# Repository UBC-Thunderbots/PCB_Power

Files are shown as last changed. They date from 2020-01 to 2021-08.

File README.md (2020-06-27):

# PCB_Power README

## Description

This repository contains Altium PCB files for UBC Thunderbots' power pcb. Anyone who wishes to push changes to this project must get permission from the current Electrical Team Lead.

## Getting Started

### Required software

1. git
2. Altium Designer

### Instructions

1. Either create a new working branch or select an existing branch other than `master`.
2. **Recursively clone** (`git clone --recurse-submodules`) your working branch of the repository to your PC (i.e. `C:/Documents/thunderbots/PCB_Power`).
3. In Altium Designer, navigate to *Preferences -> Data Management -> Version Control* and ensure **SVN - Subversion** is enabled and **Version 1.9** is selected.
4. In Altium Designer, navigate to *Preferences -> Data Management -> Design Repositories*.
5. Within *Design Repositories* click on on *Connect To* -> **SVN**.
6. In the dialogue box that comes up, fill in the following information:

Field|Selection/Input
---|---
Name|PCB_Power
Default Checkout Path|location of local repository (i.e. `C:/Documents/thunderbots/PCB_Power`)
Method|https
Server|github.com
Server Port|Default
Repository Subfolder|/UBC-Thunderbots/PCB_Power
User Name|*your github login username*
Password|*your github login password*

7. Click **Test**.

After your repository is connected, you can add or remove files like a regular Altium Project folder and then commit and push your changes to the remote repository.

[Reference](https://forum.live.altium.com/#posts/235981/718003)

### Altium_Libraries Submodule Integration

To enforce component and board compatibility, the Altium_Libraries repository is integrated as a submodule. Before making changes to a project, **ensure that your local `Altium_Libraries/` submodule is current**. This can be done using `git submodule update` in git bash.

## Repository Structure

At the highest level, there should be the most up to date board revisions, (e.g.
`power-v1.0/`), `archive/`, and `Altium_Libraries/`. Any previous versions should be placed in `archive/`. Every board revision directory should abide by the following structure:

```
<name-v#>/
├── doc/
│   ├── <name>.pdf
│   └── <name>.xslx or <name>.csv
├── pcb/
│   ├── guidelines/
│   ├── <name>.PrjPCB
│   ├── <name>.SchDoc
│   └── <name>.PcbDoc
└── sim/
```

### doc/

For documentation and relevant non-simulation and layout files. This includes PDFs of the design and bills of materials (`*.xlsx` or `.csv` format).

### pcb/

For any PCB design software files related to the schematic capture and PCB layout of board. This includes schematic and PCB layout guidelines (`guidelines/`).

### sim/

For any simulation files related to the PCB design here.

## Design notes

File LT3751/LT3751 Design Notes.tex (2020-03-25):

\documentclass{article}
\usepackage{amsmath}
\usepackage{fullpage}
\usepackage{graphicx}

\title{LT3751 Design Notes}
\author{Graham Whyte}

\begin{document}
	\maketitle
	\noindent This document will contain the design process for the LT3751 flyback converter. It is to be used alongside (not in place of) the LT3751 data sheet. Thunderbots uses this converter as a 24V - 240V capacitor charger. \\
	
	\begin{figure}[h!]
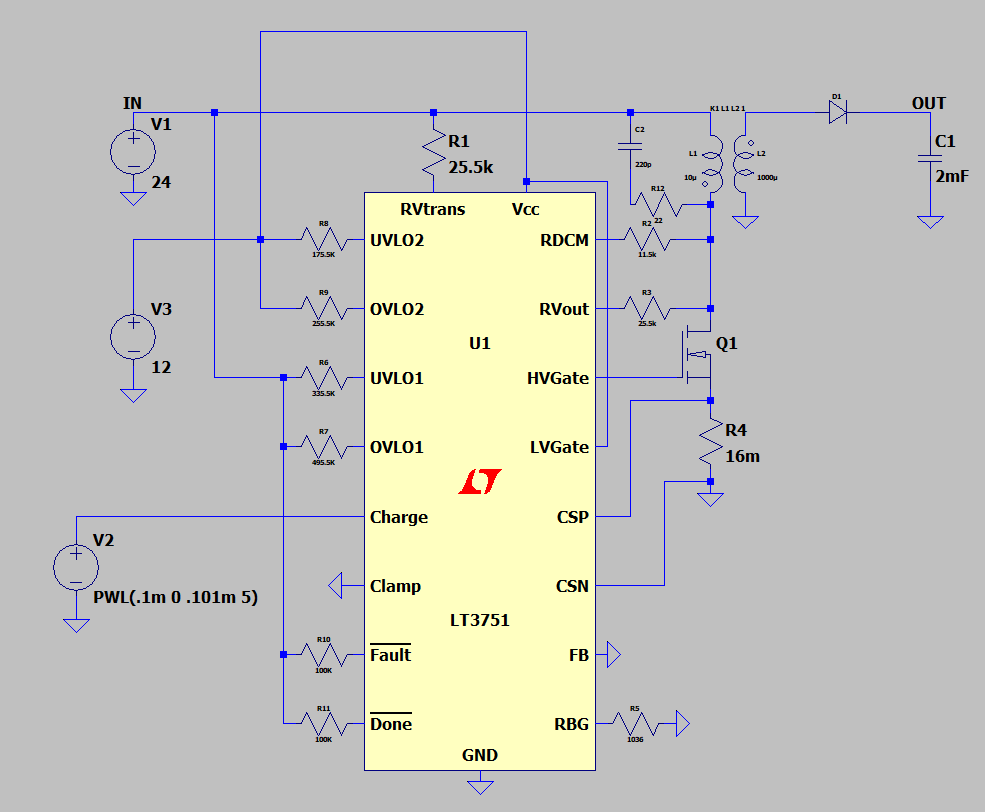
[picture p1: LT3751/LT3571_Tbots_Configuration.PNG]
		
	\end{figure}
	
	\noindent The following variables were selected as design parameters:
	
	\begin{table}[h]
		\centering
		\begin{tabular}{lll}
			\textbf{Parameter}   & \textbf{Description}                      & \textbf{Value} \\
			\hline
			$V_{trans}$ & Transformer supply voltage       & 24V   \\
			$V_{out}$   & Output voltage                   & 240V  \\
			$C_{out}$   & Output capacitance               & 2mF   \\
			$I_{pk}$    & Peak transformer primary current & 10A  \\
			$VCC$		& Supply Voltage				   & 12V
		\end{tabular}
		\centering
	\end{table}
	
	\section{Pins}
	This section will briefly describe each pin and the calculations of any necessary components.\\
	
	\noindent \textbf{Note: Resistor values are calculated values and need to be updated with standard resistor values}
	
	\subsection{RVtrans}
	RVtrans is used as the transformer supply sense pin. The resistor $R_{trans}$ is placed between $V_{trans}$ and the pin. See Section 2 for instructions on setting $RV_{trans}$.
	
	\subsection{UVLO1, OVLO1, UVLO2, OVLO2}
	These four pins serve similar purposes, so they will be covered in the same section. UVLO1 and OVLO1 are the $V_{trans}$ undervoltage/overvoltage detection pins and will raise a fault signal when $V_{trans}$ drops below 18V or goes above 26V. They are connected to $V_{trans}$ via $R_{UVLO1}$ and $R_{OVLO1}$, which are calculated as per page 7 of the data sheet:
	\[R_{UVLO1} = \dfrac{V_{UVLO1} - 1.225V}{50\mu A} = \dfrac{18V - 1.225V}{50\mu A} = 335.5k\Omega\]
	\[R_{OVLO1} = \dfrac{V_{OVLO1} - 1.225V}{50\mu A} = \dfrac{26V - 1.225V}{50\mu A} = 495.5k\Omega\]
	UVLO2 and OVLO2 are the VCC undervoltage/overvoltage detection pins and will raise a fault signal when $VCC$ drops below 10V or goes above 14V. They are connected to $VCC$ via $R_{UVLO2}$ and $R_{OVLO2}$ which are calculated as follows:
	\[R_{UVLO2} = \dfrac{V_{UVLO2} - 1.225V}{50\mu A} = \dfrac{10V - 1.225V}{50\mu A} = 175.5k\Omega\]
	\[R_{OVLO2} = \dfrac{V_{OVLO2} - 1.225V}{50\mu A} = \dfrac{14V - 1.225V}{50\mu A} = 255.5k\Omega\]
	
	\subsection{Fault}
	This (active low) pin goes low when an undervoltage or overvoltage condition occurs and all switching will be disabled. The charge pin must be toggled to reset this signal. This pin must be pulled up to $V_{trans}$ or $VCC$ via a 100k$\Omega$ resistor.
	
	\subsection{Done}
	This (active low) pin goes low when the target output voltage is reached or the fault pin goes low. The charge pin must be toggled to reset this signal. This pin must be pulled up to $V_{trans}$ or $VCC$ via a 100k$\Omega$ resistor.
	
	\subsection{Charge}
	Drive pin higher than 1.5V to start charging. Bring to below 0.3V to stop charging. This pin is directly controlled by the microcontroller.
	
	\subsection{Clamp}
	Clamps the gate driver pin voltage. Clamp is set to 5.6V if this pin is connected to $VCC$ and 10.5V if connected to ground. In our implementation, $V_{GS}$ of our NMOS transistor is 10V so Clamp is connected to GND.
	
	\subsection{FB}
	Feedback regulation pin. The voltage of this pin determines whether the LT3571 is used as a no-load voltage regulator, heavy load voltage regulator, or capacitor charger. We connect this pin to ground for capacitor charger mode.
	
	\subsection{CSN and CSP}
	Negative and positive NMOS source current sense pins. Connect CSP to the source of the external transistor and CSN to ground, then connect a source resistor between CSP and CSN to complete the circuit. The value of this sense resistor is important as it sets the maximum value of the source current through the transistor, which by extension is the current through the transformer primary ($I_{pk}$). This resistor is calculated as follows:
	\[R_{CS} = \dfrac{106mV}{I_{pk}} = \dfrac{106mV}{10A} = 16m\Omega\]
	
	\subsection{VCC}
	12V input from the voltage regulator. Bypass with a XR5 ceramic cap because the data sheet says so.
	
	\subsection{LVGate}
	Low voltage gate pin. If $VCC$ is less than 8V, connect to external transistor gate. Otherwise connect to $VCC$. Our $VCC$ is 12V so this pin is connected to $VCC$. 
	
	\subsection{HVGate}
	High voltage gate pin. Connect to external transistor gate. Will drive gate voltage to within $VCC$-2V. Gets clamped based on the state of the Clamp pin.
	
	\subsection{RBG}
	This pin is really important because it sets the output voltage! Connect to ground via the $R_{BG}$ resistor. See section 2 for instructions on setting this resistor value.
	
	\subsection{RVout}
	Output voltage sense pin. Pretty self-explanatory. Connect to the external NMOS drain via the $R_{out}$ resistor. See section 2 for instructions on setting this resistor value.
	
	\subsection{RDCM}
	Discontinuous mode sense pin. Determines when to initiate the next switch cycle. Connect to the external NMOS drain via the $R_{DCM}$ resistor. See section 2 for instructions on setting this resistor value.
	
	\subsection{GND}
	Don't worry about it.
	
	\section{External Resistors}
	\subsection{RTrans, Rout, and RDCM}
	The values of $R_{trans}, R_{out}, \text{and } R_{DCM}$ are set based on $V_{trans}$ and $\Delta V_{Drain}$, where $\Delta V_{Drain}$ is the difference between $V_{Drain}$ (the drain of the external NMOS) and $V_{trans}$. $V_{Drain}$ is just $V_{out}$ + $V_{out}$ reflected back over the primary. 
	\[V_{Drain} = V_{trans} + \dfrac{V_{out}}{n} = 24V + \dfrac{240V}{10} = 48V\]
	We use this value for $\Delta V_{Drain}$:
	\[\Delta V_{Drain} = V_{Drain} - V_{trans} = 48V - 24V = 24V\]
	and compare it to Table 2 in the data sheet (pg 17):
	
	\begin{figure}[h!]
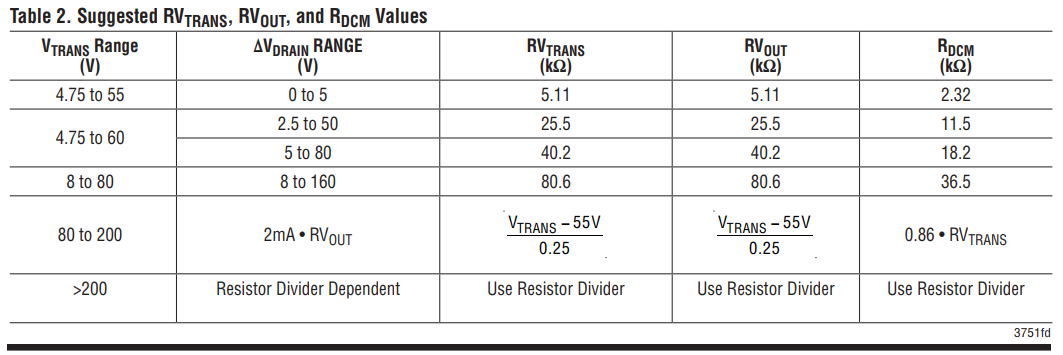
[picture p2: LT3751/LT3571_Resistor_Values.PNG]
		
	\end{figure}

	\noindent Based on the table, $R_{trans} = 25.5k\Omega, R_{out} = 25.5k\Omega, \text{and } R_{DCM} = 11.5k\Omega$. These are also the values RoboJackets use so that's probably a good sign.

	\subsection{RBG}
	With the other resistors selected, $R_{BG}$ is calculated as follows (as per pg 45 of the data sheet):
	\[R_{BG} = 0.98N\dfrac{RV_{out}}{V_{out} + V_{diode}} = 0.98(10)\dfrac{25.5k\Omega}{240V + 1.7V} = 1033.9\Omega\]
	Where N is based on the flyback transformer (section 3.1) and $V_{diode}$ is the forward voltage of the output diode (section 3.2).
	
	\section{External Components}
	\subsection{Flyback Transformer}
	$I_{pk}$ is the main criteria for selecting the transformer. The CoilCraft DA-2034-AL is one of the transformers recommended by the LT3751 manufacturers (table 1 of the data sheet). It is the current frontrunner because of its ability to handle up to 10A on the primary, 1:10 ratio, and relatively small size. \textbf{Not available on digikey though (is available on Mouser).} This transformer is currently used by RoboJackets, while the similar CoilCraft DA-2032-AL is used by Mannheim ($I_{pk} = 5A$ for this transformer).
	\subsection{Output Diode}
	The output diode is selected based on the maximum repetitive reverse voltage ($V_{RRM}$) and the average forward current $I_{Av}$. The diode must meet the following requirements:
	\[V_{RRM} > V_{out} + N*V_{trans} = 240V + 10(24V)  = 480V\]
	\[I_{Av} > \dfrac{I_pk}{2N} = \dfrac{10A}{2*20} = 0.5A\]  
	The Fairchild ES3J is one of the diodes recommended by the LT3751 manufacturers (table 4 in the data sheet). It meets our requirements and has a low $t_{rr}$.
	\subsection{External NMOS}
	The Fairchild FDS2582 is one of the transistors recommended by the LT3751 manufacturers (table 3 in the data sheet).
	\subsection{RC Snubber Circuit}
	The purpose of the RC snubber circuit is to reduce the effect of the transformer leakage inductance. The transformer is not ideal; not all energy will be transferred from one coil to the other. When the MOSFET turns off, this energy needs to go somewhere. Otherwise, we will have a large voltage spike on the drain of the MOSFET, which may be enough to damage it. The voltage spike could also be enough for the comparator to think the capacitor bank is done charging, even if it's actually nowwhere near the charge voltage.\\\\
	Simulating the LT3751 with the non-ideal transformer was challenging, where seemingly impossible voltage spikes were noticed. After talking with Will from RoboJackets, I think that the spice model for the LT3751 is simply not designed to model a non-ideal transformer. Additionally, this simulation (and possibly the LT3751 itself) is incompatible with industry standard RCD or Zener snubber circuits.\\\\ 
	For the time being, our approach is to leave footprints for the RC snubber on the PCB and populate as needed. Will said that the transformer leakage inductance was small compared to the inductances caused by the high currents, and they were able to test different combinations of R and C in the snubber. We will use the same approach for the time being. 
\end{document}

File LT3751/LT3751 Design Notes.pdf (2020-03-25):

# LT3751 Design Notes

Graham Whyte

March 24, 2020

This document will contain the design process for the LT3751 flyback converter. It is to be used alongside (not in place of) the LT3751 data sheet. Thunderbots uses this converter as a 24V - 240V capacitor charger.


The following variables were selected as design parameters:

1

Parameter | Description | Value
Vtrans | Transformer supply voltage | 24V
Vout | Output voltage | 240V
Cout | Output capacitance | 2mF
Ipk | Peak transformer primary current | 10A
V CC | Supply Voltage | 12V

## 1 Pins

This section will briefly describe each pin and the calculations of any necessary components.

Note: Resistor values are calculated values and need to be updated with standard resistor values

### 1.1 RVtrans

RVtrans is used as the transformer supply sense pin. The resistor Rtrans is placed between Vtrans and the pin. See Section 2 for instructions on setting RVtrans.

### 1.2 UVLO1, OVLO1, UVLO2, OVLO2

These four pins serve similar purposes, so they will be covered in the same section. UVLO1 and OVLO1 are the Vtrans undervoltage/overvoltage detection pins and will raise a fault signal when Vtrans drops below 18V or goes above 26V. They are connected to Vtrans via RUV LO1 and ROV LO1, which are calculated as per page 7 of the data sheet:

RUV LO1 =

VUV LO1 − 1.225V
50µA | =

18V − 1.225V
50µA = 335.5kΩ

ROV LO1 =

VOV LO1 − 1.225V
50µA | =

26V − 1.225V
50µA = 495.5kΩ

UVLO2 and OVLO2 are the VCC undervoltage/overvoltage detection pins and will raise a fault signal when V CC drops below 10V or goes above 14V. They are connected to V CC via RUV LO2 and ROV LO2 which are calculated as follows:

RUV LO2 =

VUV LO2 − 1.225V
50µA | =

10V − 1.225V
50µA = 175.5kΩ

ROV LO2 =

VOV LO2 − 1.225V
50µA | =

14V − 1.225V
50µA = 255.5kΩ

### 1.3 Fault

This (active low) pin goes low when an undervoltage or overvoltage condition occurs and all switching will be disabled. The charge pin must be toggled to reset this signal. This pin must be pulled up to Vtrans or V CC via a 100kΩ resistor.

### 1.4 Done

This (active low) pin goes low when the target output voltage is reached or the fault pin goes low. The charge pin must be toggled to reset this signal. This pin must be pulled up to Vtrans or V CC via a 100kΩ resistor.

2

### 1.5 Charge

Drive pin higher than 1.5V to start charging. Bring to below 0.3V to stop charging. This pin is directly controlled by the microcontroller.

### 1.6 Clamp

Clamps the gate driver pin voltage. Clamp is set to 5.6V if this pin is connected to V CC and 10.5V if connected to ground. In our implementation, VGS of our NMOS transistor is 10V so Clamp is connected to GND.

### 1.7 FB

Feedback regulation pin. The voltage of this pin determines whether the LT3571 is used as a no-load voltage regulator, heavy load voltage regulator, or capacitor charger. We connect this pin to ground for capacitor charger mode.

### 1.8 CSN and CSP

Negative and positive NMOS source current sense pins. Connect CSP to the source of the external transistor and CSN to ground, then connect a source resistor between CSP and CSN to complete the circuit. The value of this sense resistor is important as it sets the maximum value of the source current through the transistor, which by extension is the current through the transformer primary (Ipk). This resistor is calculated as follows:
RCS =

106mV

Ipk

=

106mV
10A

= 16mΩ

### 1.9 VCC

12V input from the voltage regulator. Bypass with a XR5 ceramic cap because the data sheet says so.

### 1.10 LVGate

Low voltage gate pin. If V CC is less than 8V, connect to external transistor gate. Otherwise connect to V CC. Our V CC is 12V so this pin is connected to V CC.

### 1.11 HVGate

High voltage gate pin. Connect to external transistor gate. Will drive gate voltage to within V CC-2V. Gets clamped based on the state of the Clamp pin.

### 1.12 RBG

This pin is really important because it sets the output voltage! Connect to ground via the RBG resistor. See section 2 for instructions on setting this resistor value.

### 1.13 RVout

Output voltage sense pin. Pretty self-explanatory. Connect to the external NMOS drain via the Rout resistor. See section 2 for instructions on setting this resistor value.

3

### 1.14 RDCM

Discontinuous mode sense pin. Determines when to initiate the next switch cycle. Connect to the external NMOS drain via the RDCM resistor. See section 2 for instructions on setting this resistor value.

### 1.15 GND

Don’t worry about it.

## 2 External Resistors

### 2.1 RTrans, Rout, and RDCM

The values of Rtrans, Rout, and RDCM are set based on Vtrans and ∆VDrain, where ∆VDrain is the difference between VDrain (the drain of the external NMOS) and Vtrans. VDrain is just Vout + Vout reflected back over the primary.

VDrain = Vtrans +

Vout
n

= 24V +

240V
10

= 48V

We use this value for ∆VDrain:

∆VDrain = VDrain − Vtrans = 48V − 24V = 24V

and compare it to Table 2 in the data sheet (pg 17):

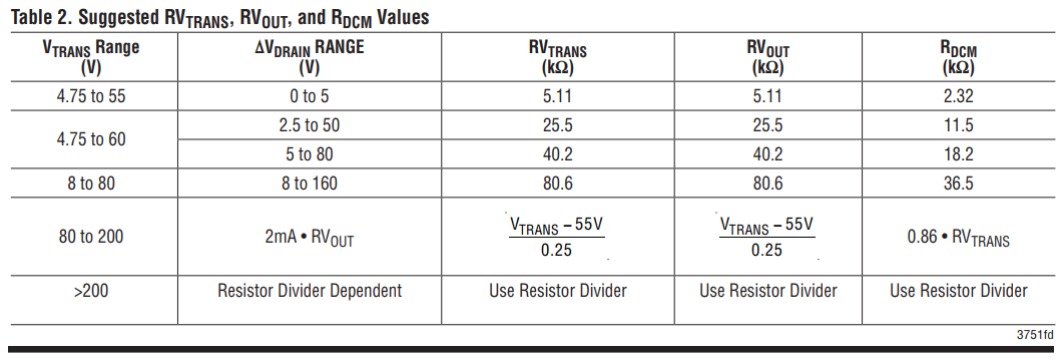
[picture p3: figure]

Based on the table, Rtrans = 25.5kΩ, Rout = 25.5kΩ, and RDCM = 11.5kΩ. These are also the values RoboJackets use so that’s probably a good sign.

### 2.2 RBG

With the other resistors selected, RBG is calculated as follows (as per pg 45 of the data sheet):

RBG = 0.98N

RVout

Vout + Vdiode

= 0.98(10) 25.5kΩ 240V + 1.7V
= 1033.9Ω

Where N is based on the flyback transformer (section 3.1) and Vdiode is the forward voltage of the output diode (section 3.2).

4

## 3 External Components

### 3.1 Flyback Transformer

Ipk is the main criteria for selecting the transformer. The CoilCraft DA-2034-AL is one of the transformers recommended by the LT3751 manufacturers (table 1 of the data sheet). It is the current frontrunner because of its ability to handle up to 10A on the primary, 1:10 ratio, and relatively small size. Not available on digikey though (is available on Mouser). This transformer is currently used by RoboJackets, while the similar CoilCraft DA-2032-AL is used by Mannheim (Ipk = 5A for this transformer).

### 3.2 Output Diode

The output diode is selected based on the maximum repetitive reverse voltage (VRRM) and the average forward current IAv. The diode must meet the following requirements:

VRRM > Vout + N ∗ Vtrans = 240V + 10(24V ) = 480V

IAv >

Ipk
2N

=

10A
2 ∗ 20

= 0.5A

The Fairchild ES3J is one of the diodes recommended by the LT3751 manufacturers (table 4 in the data sheet). It meets our requirements and has a low trr.

### 3.3 External NMOS

The Fairchild FDS2582 is one of the transistors recommended by the LT3751 manufacturers (table 3 in the data sheet).

### 3.4 RC Snubber Circuit

The purpose of the RC snubber circuit is to reduce the effect of the transformer leakage inductance. The transformer is not ideal; not all energy will be transferred from one coil to the other. When the MOSFET turns off, this energy needs to go somewhere. Otherwise, we will have a large voltage spike on the drain of the MOSFET, which may be enough to damage it. The voltage spike could also be enough for the comparator to think the capacitor bank is done charging, even if it’s actually nowwhere near the charge voltage.

Simulating the LT3751 with the non-ideal transformer was challenging, where seemingly impossible voltage spikes were noticed. After talking with Will from RoboJackets, I think that the spice model for the LT3751 is simply not designed to model a non-ideal transformer. Additionally, this simulation (and possibly the LT3751 itself) is incompatible with industry standard RCD or Zener snubber circuits.

For the time being, our approach is to leave footprints for the RC snubber on the PCB and populate as needed. Will said that the transformer leakage inductance was small compared to the inductances caused by the high currents, and they were able to test different combinations of R and C in the snubber. We will use the same approach for the time being.

5

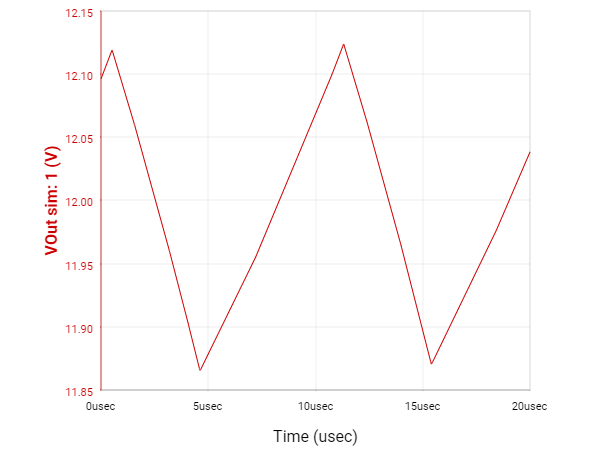
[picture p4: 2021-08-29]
power-v3.3/doc/12V-dc_dc-converter-design/sim_vout.jpg

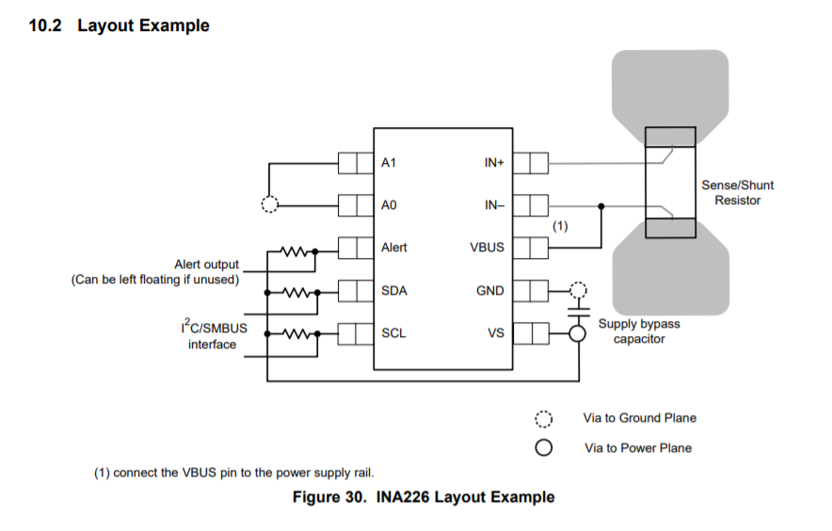
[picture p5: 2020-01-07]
power-v3.3/doc/INA226_sch.PNG

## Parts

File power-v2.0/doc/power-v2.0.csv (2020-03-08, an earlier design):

Comment | Designator | Description | Digikey | Digikey Link | MF | MP | Package | Quantity | Rating
100nF | C1, C3, C6 | CAP CER 0.1UF 50V X7R 0805 | 311-1140-1-ND | https://www.digikey.ca/products/en?keywords=311-1140-1-ND | Yageo | CC0805KRX7R9BB104 | 805 | 3 | 50V
10uF | C7, C8 | CAP CER 10UF 50V X7R 1210 | 1276-3388-1-ND | https://www.digikey.ca/product-detail/en/samsung-electro-mechanics/CL32B106KBJNNWE/1276-3388-1-ND/3891474 | Samsung Electro-Mechanics | CL32B106KBJNNWE | 1210 | 2 | 50V
8.2nF | C9 | CAP CER 8200PF 50V X7R 0805 | 399-9275-1-ND | https://www.digikey.ca/product-detail/en/kemet/C0805C822K5RACTU/399-9275-1-ND/3522793 | KEMET | C0805C822K5RACTU | 805 | 1 | 50V
47uF | C10, C11 | CAP CER 47UF 6.3V X7R 1210 | 490-4844-1-ND | https://www.digikey.ca/product-detail/en/murata-electronics/GCM32ER70J476KE19L/490-4844-1-ND/1763982 | Murata Electronics | GCM32ER70J476KE19L | 1210 | 2 | 6.3V
10pF | C12 | CAP CER SMD 0603 10PF 10% X7R 50 | 399-17562-1-ND | https://www.digikey.ca/product-detail/en/kemet/C0603C100K5RAC7867/399-17562-1-ND/8572562 | KEMET | C0603C100K5RAC7867 | 603 | 1 | 50V
1nF | C13 | CAP CER 1000PF 50V X7R 0805 | 311-1127-1-ND | https://www.digikey.ca/products/en?keywords=311-1127-1-ND | Yageo | CC0805KRX7R9BB102 | 805 | 1 | 50V
4.7uF | C14, C15 | CAP CER 4.7UF 25V X5R 0805 | 1276-2873-1-ND | https://www.digikey.ca/product-detail/en/samsung-electro-mechanics/CL21B475KOFNNNE/1276-2873-1-ND/3890959 | Samsung Electro-Mechanics | CL21B475KOFNNNE | 805 | 2 | 16V
MMSZ5245B-TP | D1 | Zener Diode 15V 500mW ±5% Surface Mount SOD-123 |  |  | ON Semiconductor | MMSZ5224BT1G | SOD-123 ON Semiconductor | 1
LED2 | D3, D4, D5 | Typical RED, GREEN, YELLOW, AMBER GaAs LED | 160-1446-1-ND | https://www.digikey.ca/products/en?keywords=160-1446-1-ND | Lite-On Inc. | LTST-C191KGKT | 603 | 3 | 2V
SBRD10200TR | D8 | Diode Schottky 200V 10A Surface Mount DPAK | 1655-1939-1-ND | https://www.digikey.ca/product-detail/en/smc-diode-solutions/SBRD10200TR/1655-1939-1-ND/8625508 | SMC Diode | SBRD10200TR | TO-252-3 SMC | 1
Fuse 20A 1206 | F1 | FUSE BOARD MOUNT 20A 32VAC 63VDC | 486-1689-6-ND | https://www.digikey.ca/product-detail/en/schurter-inc/3413.0331.22/486-1689-6-ND/2870024 | Schurter Inc. | 3413.0331.22 |  | 1 | 20A
CONN HEADER VERT 6POS 3.96MM | JM1, JM2, JM3, JM4 | Connector Header Through Hole 6 position 0.156 (3.96mm)" | https://www.digikey.ca/product-detail/en/te-connectivity-amp-connectors/1877285-6/A99849-ND/2000097 | A99849-ND | TE Connectivity | 1877285-6 |  | 4
SRU1048-8R2Y | L1 | FIXED IND 8.2UH 4.6A 15 MOHM SMD | SRU1048-8R2YCT-ND | https://www.digikey.ca/en/products/detail/bourns-inc/SRU1048-8R2Y/2352912 | Bourns Inc. | SRU1048-8R2Y | Nonstandard | 1
XT60 | P1 | XT60 CONNECTORS FEMALE PAIR | 1568-1816-ND | https://www.digikey.ca/product-detail/en/sparkfun-electronics/PRT-10474/1568-1816-ND/8258064 | SparkFun Electronics | PRT-10474 | XT60 | 1
Header 2X2 | P3 | Header, 2-Pin, Dual row |  |  |  |  |  | 1
Header 4X2 | PN | Header, 4-Pin, Dual row |  |  |  |  |  | 1
AON6407 | Q1, Q2 | P-Channel 30V 32A (Ta), 85A (Tc) 7.3W (Ta), 83W (Tc) Surface Mount 8-DFN (5x6) | 785-1421-1-ND | https://www.digikey.ca/product-detail/en/alpha-omega-semiconductor-inc/AON6407/785-1421-1-ND/3466800 | Alpha & Omega Semiconductor Inc. | AON6407 | 8-PowerSMD | 2
1.96K | R2, R13 | RES SMD 1.96K OHM 1% 1/8W 0805 | P1.96KCCT-ND | https://www.digikey.ca/product-detail/en/panasonic-electronic-components/ERJ-6ENF1961V/P1.96KCCT-ND/119041 | Panasonic Electronic Components | ERJ-6ENF1961V | 805 | 2 | 0.125W
270 | R3 | RES SMD 270 OHM 5% 1/8W 0805 | 311-270ARCT-ND | https://www.digikey.ca/product-detail/en/yageo/RC0805JR-07270RL/311-270ARCT-ND/731238 | Yageo | RC0805JR-07270RL | 805 | 1 | 0.125W
110 | R4 | RES SMD 110 OHM 1% 1/8W 0805 | 311-110CRCT-ND | https://www.digikey.ca/product-detail/en/yageo/RC0805FR-07110RL/311-110CRCT-ND/730506 | Yageo | RC0805FR-07110RL | 805 | 1 | 0.125W
100k | R5, R17 | RES SMD 100K OHM 1% 1/8W 0805 | 311-100KCRCT-ND | https://www.digikey.ca/products/en?keywords=311-100KCRCT-ND | Yageo | RC0805FR-07100KL | 805 | 2 | 0.125W
10 | R6, R7 | RES SMD 10 OHM 1% 1/8W 0805 | 311-10.0CRCT-ND | https://www.digikey.ca/product-detail/en/yageo/RC0805FR-0710RL/311-10.0CRCT-ND/730481 | Yageo | RC0805FR-0710RL | 805 | 2 | 0.125W
10k | R8, R9, R10, R11, R12 | RES SMD 10K OHM 1% 1/8W 0805 | 311-10.0KCRCT-ND | https://www.digikey.ca/products/en?keywords=311-10.0KCRCT-ND | Yageo | RC0805FR-0710KL | 805 | 5 | 0.125W
10.2k | R14 | RES SMD 10.2K OHM 1% 1/8W 0805 | P10.2KCCT-ND | https://www.digikey.ca/product-detail/en/panasonic-electronic-components/ERJ-6ENF1022V/P10.2KCCT-ND/119251 | Panasonic Electronic Components | ERJ-6ENF1022V | 805 | 1 | 0.125W
24.3K | R15 | RES SMD 24.3K OHM 1% 1/8W 0805 | 311-24.3KCRCT-ND | https://www.digikey.ca/product-detail/en/yageo/RC0805FR-0724K3L/311-24.3KCRCT-ND/730705 | Yageo | RC0805FR-0724K3L | 805 | 1 | 0.125W
2mOhm | Rshunt | RES 0.002 OHM 1% 1W 1206 | 696-1370-1-ND | https://www.digikey.ca/product-detail/en/riedon/CSR1206-0R002F1/696-1370-1-ND/2813303 | Riedon | CSR1206-0R002F1 | 1206 | 1 | 0.125W
SPST Rocker | S1 | Rocker Switch SPST 10A (AC) 125V Panel Mount, Snap-In | CH755-ND | https://www.digikey.ca/product-detail/en/zf-electronics/SRB22A2FBBNN/CH755-ND/446021 | ZF Electronics | SRB22A2FBBNN |  | 1 | 10A 125V
INA226AIDGSR | U1 | 36-V, Bi-Directional, Ultra-High Accuracy, Low-/High-Side, I2C Out Current/Power Monitor w/ Alert 10-VSSOP -40 to 125 | 296-29034-2-ND | https://www.digikey.ca/product-detail/en/texas-instruments/INA226AIDGSR/296-29034-2-ND/2687236 | Texas Instruments | INA226AIDGSR | MSOP-10 Texas Instruments | 1
TPS54331 | U3 | Buck Switching Regulator IC Positive Adjustable 0.8V 1 Output 3A 8-SOIC _0.154, 3.90mm Width_ | 296-39419-1-ND | https://www.digikey.ca/product-detail/en/texas-instruments/TPS54331DDAR/296-39419-1-ND/5143369 | Texas Instruments | TPS54331DDAR | 8-PowerSOIC | 1
ZLDO1117K33TC | U4 | Linear Voltage Regulator IC Positive Fixed 1 Output 1A TO-252-3 | ZLDO1117K33DIDKR-ND | https://www.digikey.ca/product-detail/en/diodes-incorporated/ZLDO1117K33TC/ZLDO1117K33DIDKR-ND/2095639 | Diodes Incorporated | ZLDO1117K33TC | TO-252-3 | 1
EMI | U5, U6 | RC (Pi) EMI Filter 2nd Order Low Pass 2 Channel R = 100Ohms, C = 19pF (Total) SOT-665 | 1727-4718-1-ND | https://www.digikey.ca/product-detail/en/nexperia-usa-inc/IP4256CZ5-W115/1727-4718-1-ND/2531158 | Nexperia USA Inc. | IP4256CZ5-W,115 | SOT-665 | 2

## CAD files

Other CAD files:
archive/power-v3.1/cad/Power_pcb.SLDPRT
power-v3.1/cad/Power_pcb.SLDPRT
archive/power-v3.1/cad/Power_pcb.DXF
power-v3.1/cad/Power_pcb.DXF

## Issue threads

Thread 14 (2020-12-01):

Capacitor Bank Charge Time

s-zheng, 2020-12-01:
With the current specified sense resistor (16mR), the charge time for a 4mF capacitor bank at 240V is ~4.3s. See the spice simulation file LT3751.asc within the LT3751 directory. The captures below show a cap bank scaled by 1/1000 for reasonable simulation times.

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

This corresponds to a transformer primary current of ~7A.
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

Preliminary napkin math indicates a sensible limit on transformer primary current to be ~20A, this is achievable with a higher wattage sense resistor of ~6-7mR and a potentially higher 20A_pk rated transformer. The [GA3459-BL or GA3460-BL](https://www.coilcraft.com/en-us/products/transformers/power-transformers/capacitor-charging/ga3459/) are only ~ 5mm larger than the current BOM part in all dimensions. The decision to utilize the larger transformers depend on saturation behaviour when pushing the DA2034 beyond its I_pk rating.

Since the new HV capacitor bank is double the size of the previous system, the voltage droop on kick is ~0.7 of the previous design (70V). Rapid recovery of the HV rail could improve consistency in multi-kick plays.

s-zheng, 2020-12-06:
The temporary placeholder mosfet FDS2582 is unsuitable even for the "lower" transformer primary current options. Will update with new part selection here.

Closed 2020-12-27.

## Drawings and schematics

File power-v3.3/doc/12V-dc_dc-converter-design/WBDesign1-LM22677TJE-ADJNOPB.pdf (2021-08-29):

## WEBENCH ® Design Report

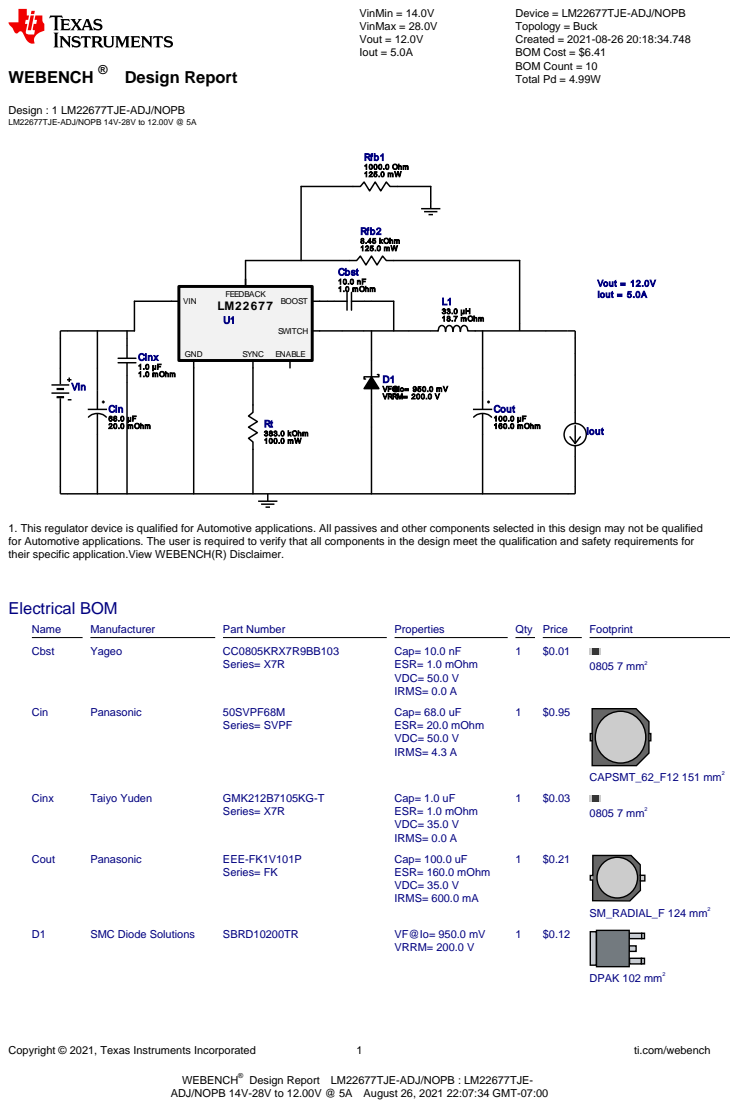
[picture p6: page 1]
Copyright © 2021, Texas Instruments Incorporated; ti.com/webench; VinMin = 14.0V VinMax = 28.0V Vout = 12.0V Iout = 5.0A; Cin; mOhm; Cinx 1.0 µF 1.0 mOhm; Rt 383.0 kOhm 100.0 mW; Cout 100.0 µF 160.0 mOhm; Vout = 12.0V Iout = 5.0A; Rfb2 8.45 kOhm 125.0 mW; Rfb1 1000.0 Ohm 125.0 mW; L1 33.0 µH 18.7 mOhm; LM22677 VIN; FEEDBACK; BOOST; SWITCH; GND; SYNC ENABLE; Cbst 10.0 nF 1.0 mOhm; D1 VF@Io= 950.0 mV VRRM= 200.0 V; Vin; Iout; Electrical BOM; Name; Manufacturer; Part Number; Properties; Qty Price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

Device = LM22677TJE-ADJ/NOPB
Topology = Buck
Created = 2021-08-26 20:18:34.748
BOM Cost = $6.41
BOM Count = 10
Total Pd = 4.99W

Design : 1 LM22677TJE-ADJ/NOPB
LM22677TJE-ADJ/NOPB 14V-28V to 12.00V @ 5A

1. This regulator device is qualified for Automotive applications. All passives and other components selected in this design may not be qualified
for Automotive applications. The user is required to verify that all components in the design meet the qualification and safety requirements for
their specific application.View WEBENCH(R) Disclaimer.

WEBENCH®
ADJ/NOPB 14V-28V to 12.00V @ 5A August 26, 2021 22:07:34 GMT-07:00

Design Report LM22677TJE-ADJ/NOPB : LM22677TJE-

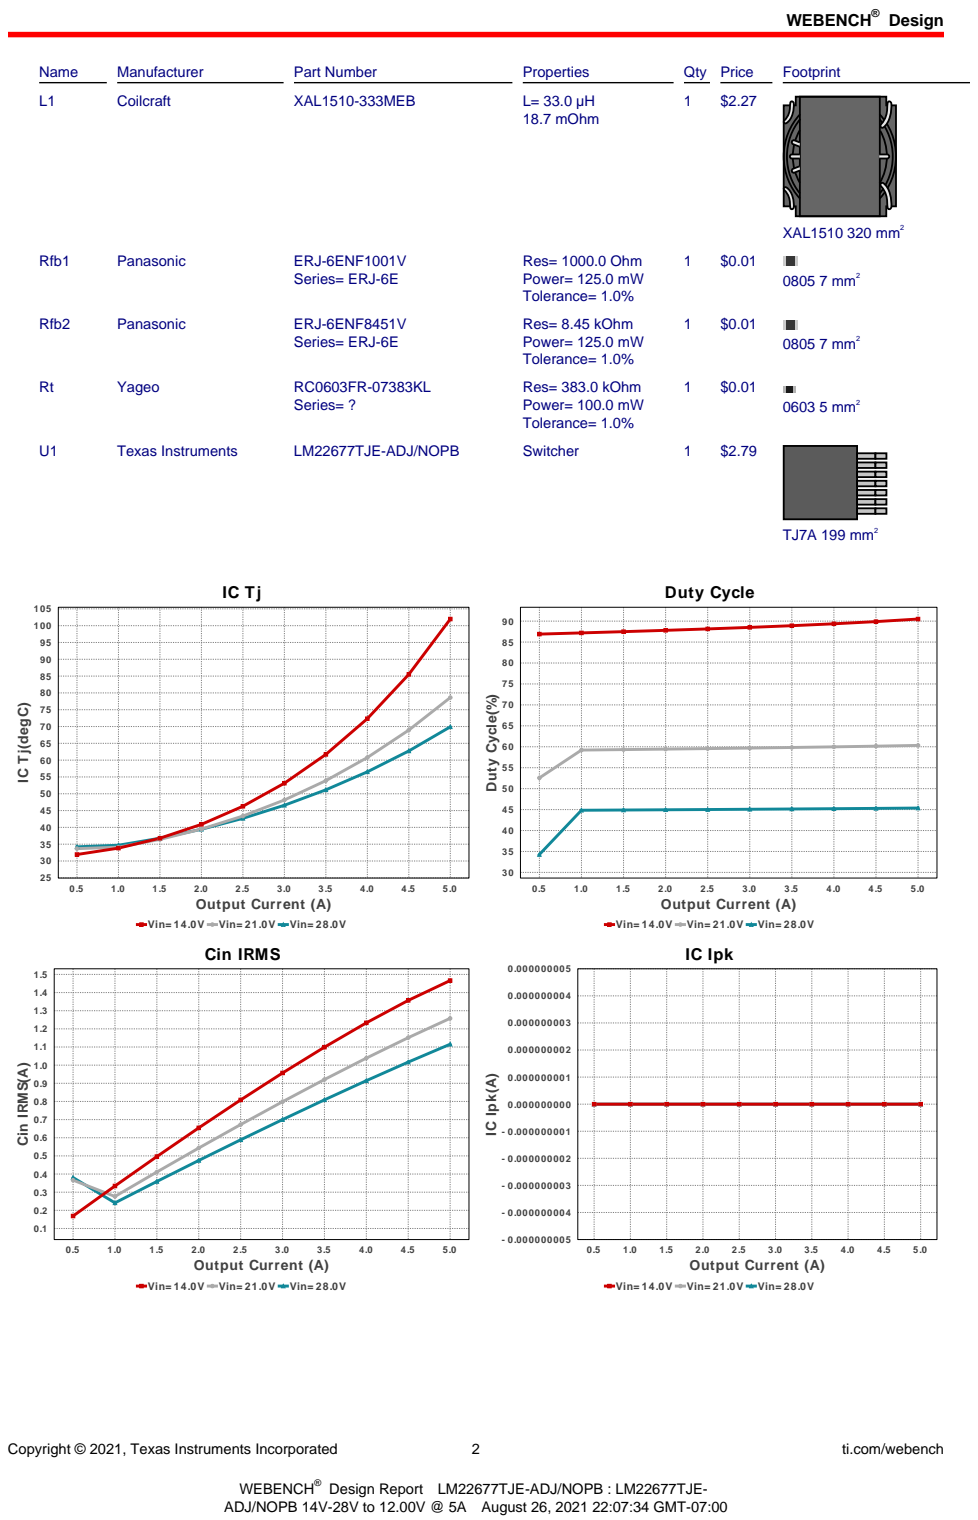
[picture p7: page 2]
Design; Copyright © 2021, Texas Instruments Incorporated; ti.com/webench; Name; Manufacturer; Part Number; Properties; Qty Price; Footprint; Coilcraft; XAL1510-333MEB; 18.7 mOhm; XAL1510 320 mm²; Rfb1; Panasonic; ERJ-6ENF1001V; Series= ERJ-6E; Res= 1000.0 Ohm Power= 125.0 mW Tolerance= 1.0%; 0805 7 mm²; Rfb2; ERJ-6ENF8451V; Res= 8.45 kOhm Power= 125.0 mW Tolerance= 1.0%; Yageo; Series= ?; Res= 383.0 kOhm Power= 100.0 mW Tolerance= 1.0%; 0603 5 mm²; Texas Instruments; LM22677TJE-ADJ/NOPB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

IC Tj(degC)

Vin= 14.0V Vin= 21.0V Vin= 28.0V
Cin IRMS

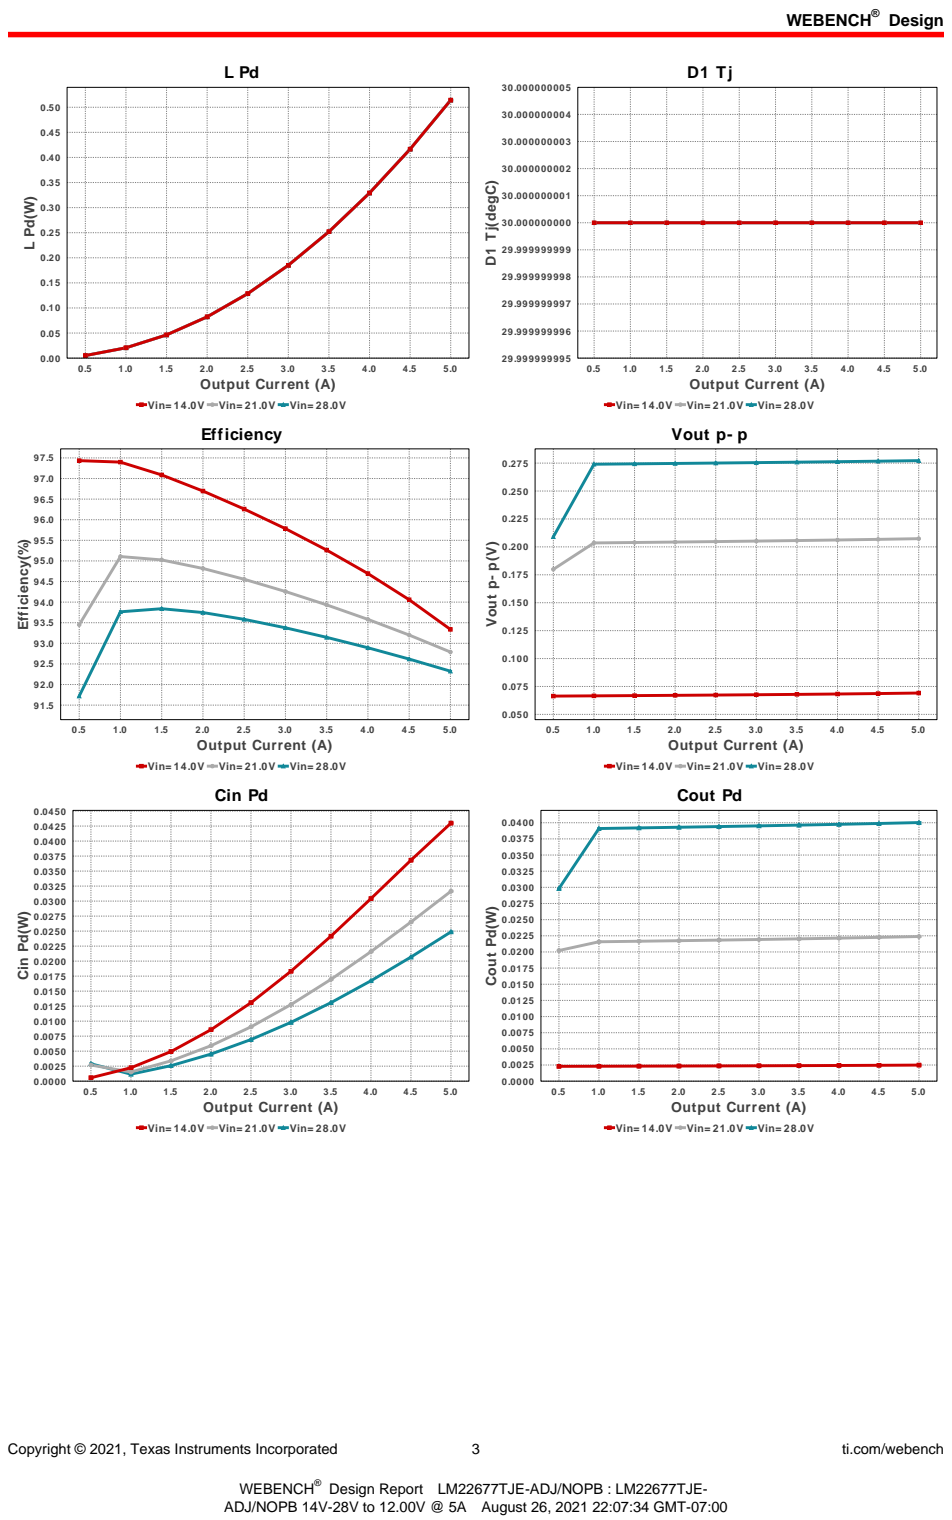
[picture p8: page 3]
Copyright © 2021, Texas Instruments Incorporated; ti.com/webench; 5.0 Output Current (A); D1 Tj(degC); Efficiency(%); Vout p- p(V); Cin Pd; Cin Pd(W); Cout Pd; Cout Pd(W)

Vin= 14.0V Vin= 21.0V Vin= 28.0V
Efficiency

Vout p- p

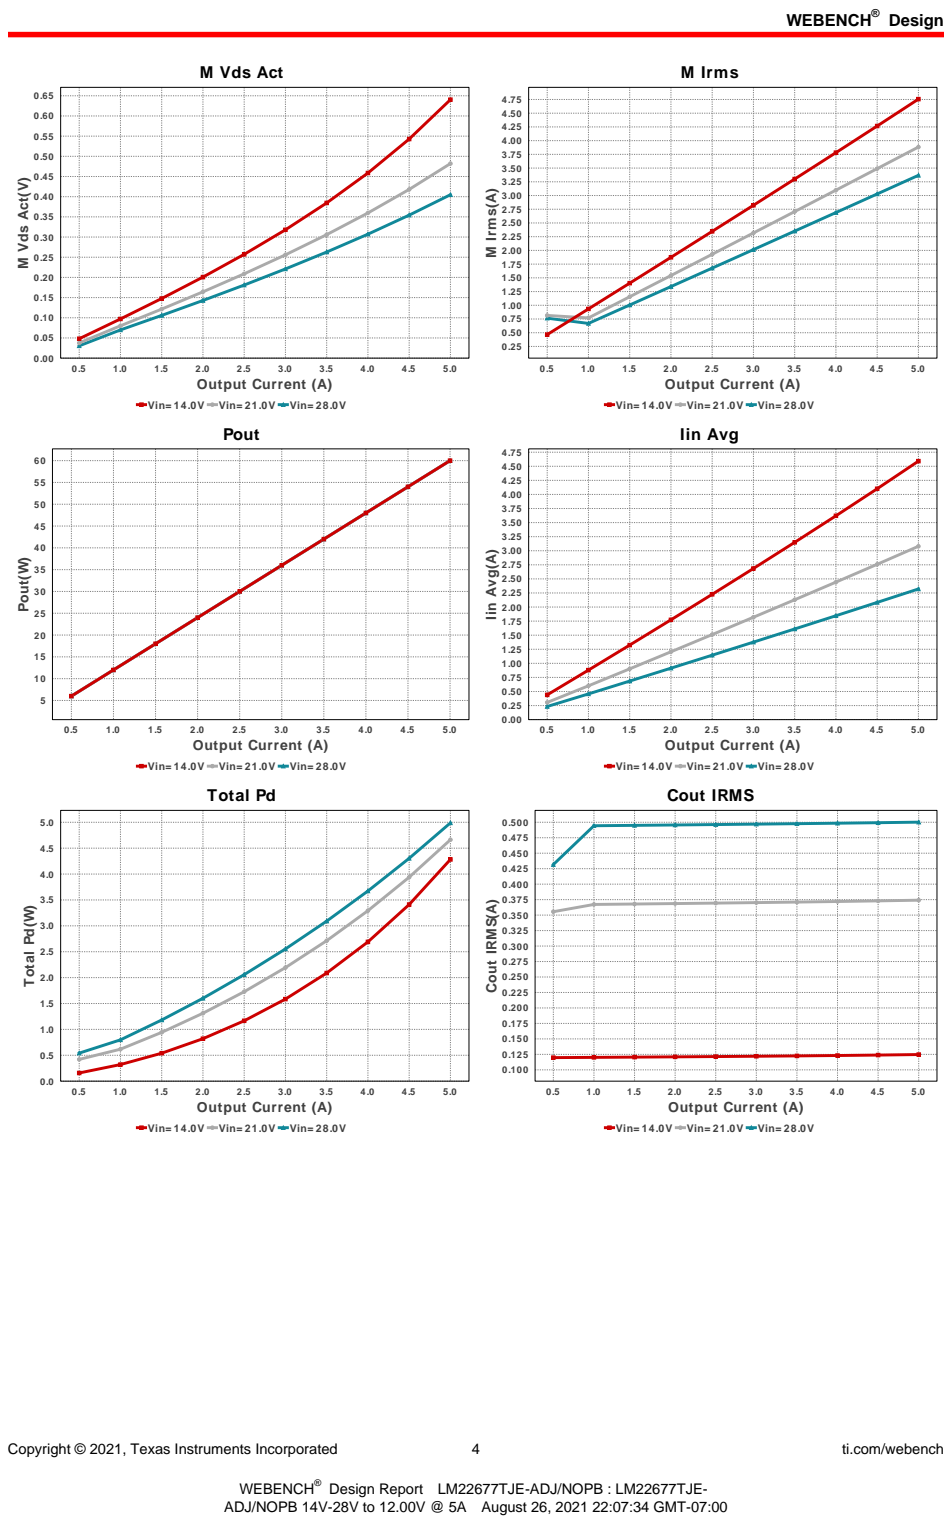
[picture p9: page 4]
Copyright © 2021, Texas Instruments Incorporated; ti.com/webench; M Vds Act; 5.0 Output Current (A); M Vds Act(V); M Irms; M Irms(A); Pout; Pout(W); Iin Avg; Iin Avg(A); Total Pd; Total Pd(W); Cout IRMS(A)

Vin= 14.0V Vin= 21.0V Vin= 28.0V

Cout IRMS

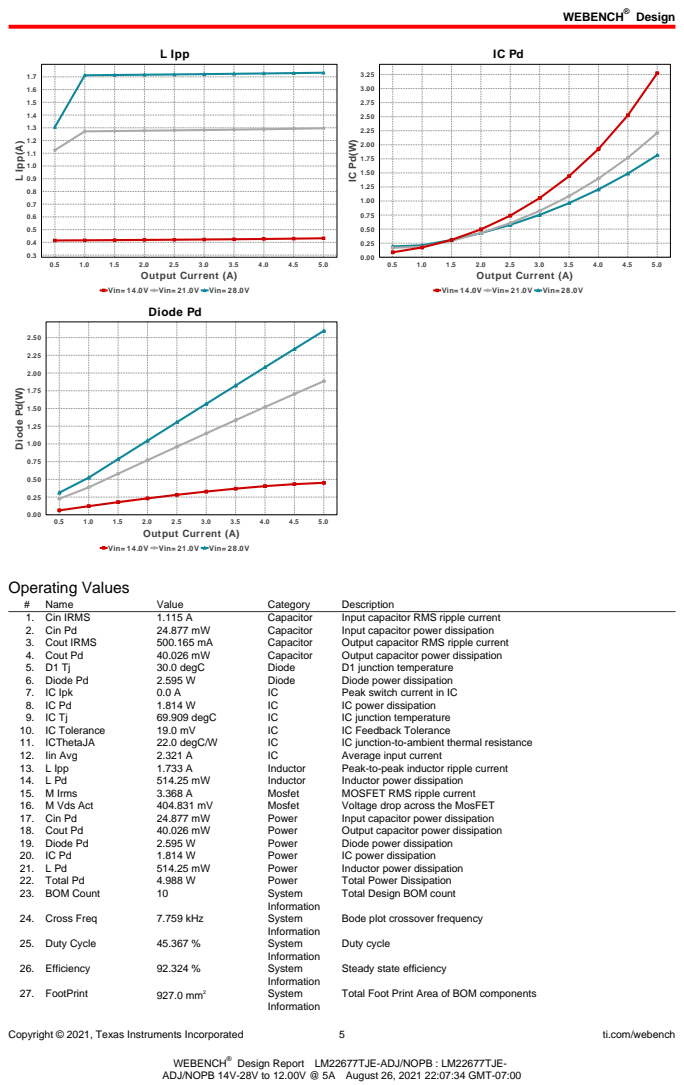
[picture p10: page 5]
Copyright © 2021, Texas Instruments Incorporated; ti.com/webench; L Ipp; 5.0 Output Current (A); L Ipp(A); Diode Pd(W); Operating Values; Name; Value; Category; Description; 1. Cin IRMS; Capacitor; Input capacitor RMS ripple current; 2. Cin Pd; Input capacitor power dissipation; 3. Cout IRMS; Output capacitor RMS ripple current; 4. Cout Pd; Output capacitor power dissipation; 30.0 degC; Diode; D1 junction temperature; 6. Diode Pd; Diode power dissipation; 7. IC Ipk; Peak switch current in IC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

Vin= 14.0V Vin= 21.0V Vin= 28.0V
Diode Pd

Total Design BOM count

Bode plot crossover frequency

Steady state efficiency

Total Foot Print Area of BOM components

Copyright © 2021, Texas Instruments Incorporated | 6 | ti.com/webench
# | Name | Value | Category | Description

28. Frequency | 126.952 kHz | System
| | | Information | Switching frequency
29. Iout | 5.0 A | System
| | | Information | Iout operating point
30. Mode | CCM | System
| | | Information | Conduction Mode
31. Phase Marg | 64.368 deg | System
| | | Information | Bode Plot Phase Margin
32. Pout | 60.0 W | System
| | | Information | Total output power
33. Total BOM | $6.41 | System
| | | Information | Total BOM Cost
34. Vin | 28.0 V | System
| | | Information | Vin operating point
35. Vout | 12.0 V | System
| | | Information | Operational Output Voltage
36. Vout Actual | 12.143 V | System
| | | Information | Achieved Vout with feedback resistor pair
37. Vout Tolerance | 3.312 % | System
| | | Information | Vout Tolerance based on IC Tolerance (no load) and voltage divider resistors if applicable
38. Vout p-p | 277.22 mV | System
| | | Information | Peak-to-peak output ripple voltage

## Design Inputs

Name | Value | Description
Iout | 5.0 | Maximum Output Current
VinMax | 28.0 | Maximum input voltage
VinMin | 14.0 | Minimum input voltage
Vout | 12.0 | Output Voltage
| base_pn | | LM22677 | Base Product Number
source | DC | Input Source Type
Ta | 30.0 | Ambient temperature


Copyright © 2021, Texas Instruments Incorporated | 7 | ti.com/webench

## Assembly
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

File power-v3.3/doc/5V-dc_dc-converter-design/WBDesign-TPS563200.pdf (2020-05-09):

## WEBENCH ® Design Report

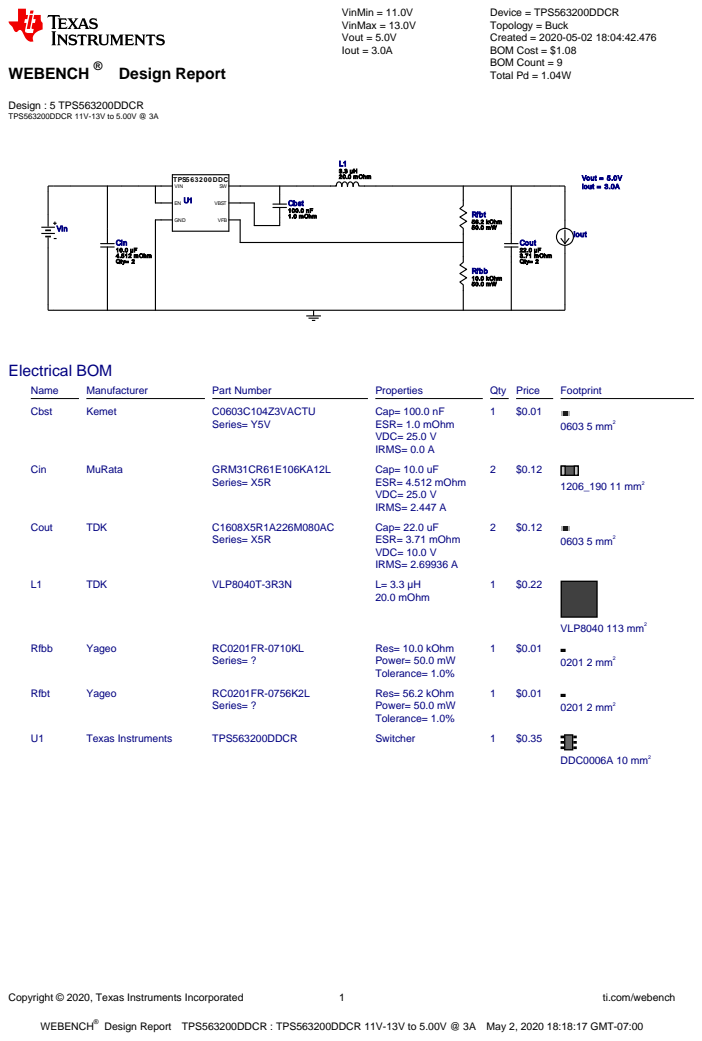
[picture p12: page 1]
Copyright © 2020, Texas Instruments Incorporated; ti.com/webench; WEBENCH®; Design : 5 TPS563200DDCR TPS563200DDCR 11V-13V to 5.00V @ 3A; VinMin = 11.0V VinMax = 13.0V Vout = 5.0V Iout = 3.0A; Device = TPS563200DDCR Topology = Buck Created = 2020-05-02 18:04:42.476 BOM Cost = $1.08 BOM Count = 9 Total Pd = 1.04W; Rfbt 56.2 kOhm 50.0 mW; Cout 22.0 µF 3.71 mOhm Qty= 2; Vout = 5.0V Iout = 3.0A; L1 3.3 µH 20.0 mOhm; Rfbb 10.0 kOhm 50.0 mW; Cin 10.0 µF 4.512 mOhm Qty= 2; TPS563200DDC; GND; VIN; VFB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

Design Report TPS563200DDCR : TPS563200DDCR 11V-13V to 5.00V @ 3A May 2, 2020 18:18:17 GMT-07:00

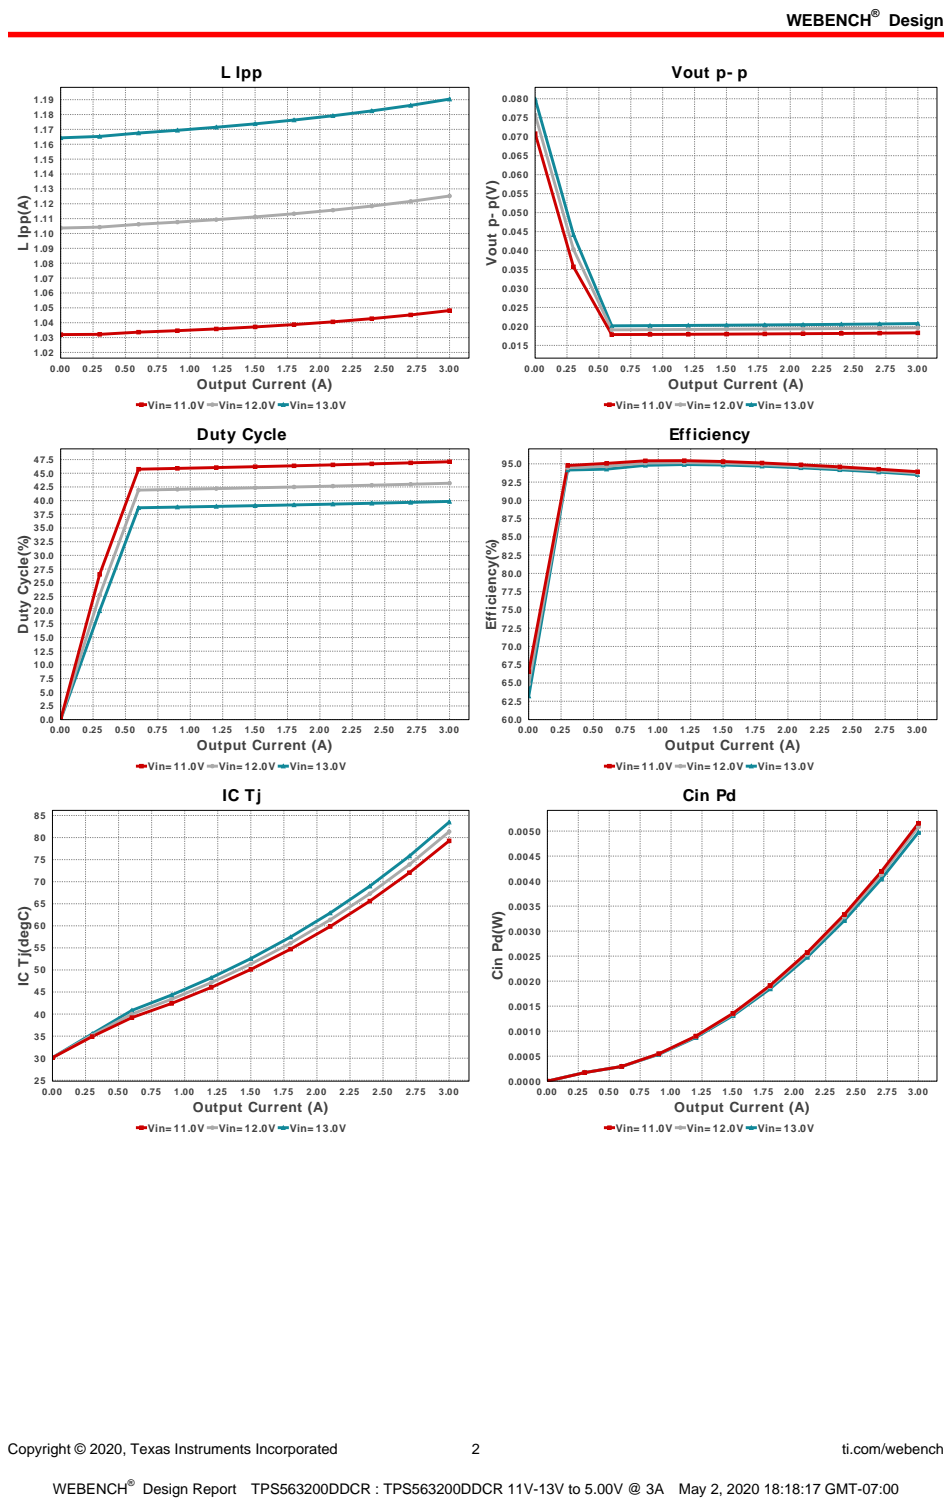
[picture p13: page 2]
Design; Copyright © 2020, Texas Instruments Incorporated; ti.com/webench; L Ipp; 0.00 0.25 0.50 0.75 1.00 1.25 1.50 1.75 2.00 2.25 2.50 2.75 3.00 Output Current (A); L Ipp(A); Vout p- p; Vout p- p(V); Duty Cycle(%); Efficiency(%); Cin Pd; Cin Pd(W)

Vin= 11.0V Vin= 12.0V Vin= 13.0V
Duty Cycle

Efficiency

IC Tj(degC)

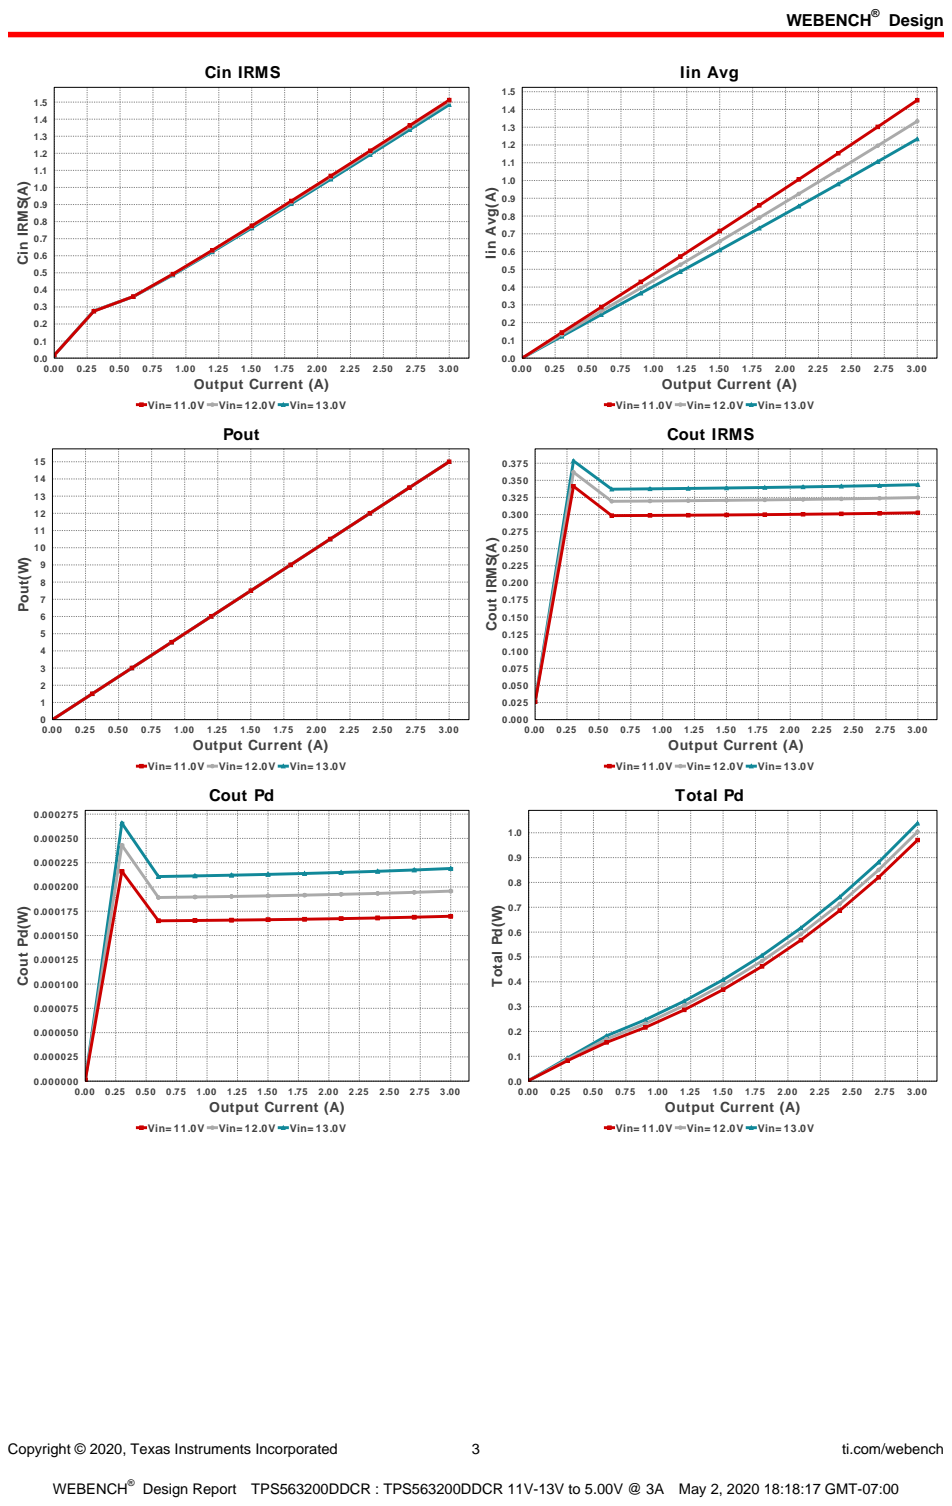
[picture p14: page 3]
Copyright © 2020, Texas Instruments Incorporated; ti.com/webench; Cin IRMS; 0.00 0.25 0.50 0.75 1.00 1.25 1.50 1.75 2.00 2.25 2.50 2.75 3.00 Output Current (A); Cin IRMS(A); Iin Avg; Iin Avg(A); Pout; Pout(W); Cout IRMS(A); Cout Pd; Cout Pd(W); Total Pd; Total Pd(W)

Vin= 11.0V Vin= 12.0V Vin= 13.0V

Cout IRMS

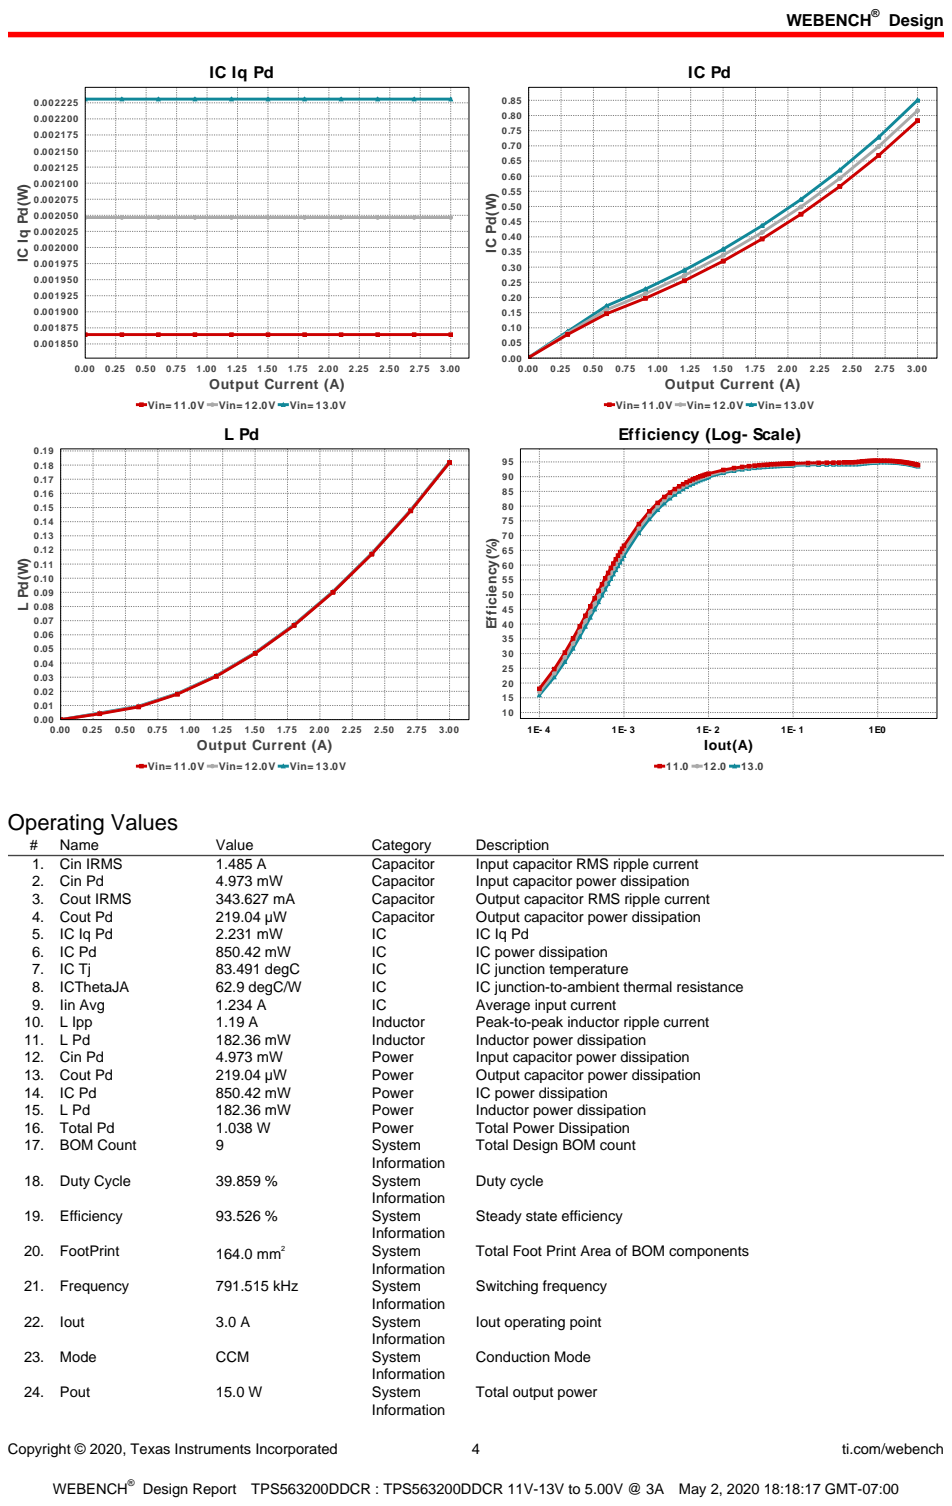
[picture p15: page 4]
Copyright © 2020, Texas Instruments Incorporated; ti.com/webench; 0.00 0.25 0.50 0.75 1.00 1.25 1.50 1.75 2.00 2.25 2.50 2.75 3.00 Output Current (A); Iout(A); Efficiency(%); Operating Values; Name; Value; Category; Description; 1. Cin IRMS; Capacitor; Input capacitor RMS ripple current; 2. Cin Pd; Input capacitor power dissipation; 3. Cout IRMS; Output capacitor RMS ripple current; 4. Cout Pd; Output capacitor power dissipation; IC power dissipation; 83.491 degC; IC junction temperature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

Vin= 11.0V Vin= 12.0V Vin= 13.0V

Efficiency (Log- Scale)

Total Design BOM count

Steady state efficiency

Total Foot Print Area of BOM components

Iout operating point

Total output power

Copyright © 2020, Texas Instruments Incorporated | 5 | ti.com/webench
# | Name | Value | Category | Description

25. Total BOM | $1.08 | System
| | | Information | Total BOM Cost
26. Vin | 13.0 V | System
| | | Information | Vin operating point
27. Vout | 5.0 V | System
| | | Information | Operational Output Voltage
28. Vout Actual | 5.031 V | System
| | | Information | Vout Actual calculated based on selected voltage divider resistors
29. Vout Tolerance | 3.053 % | System
| | | Information | Vout Tolerance based on IC Tolerance (no load) and voltage divider resistors if applicable
30. Vout p-p | 20.759 mV | System
| | | Information | Peak-to-peak output ripple voltage

## Design Inputs

Name | Value | Description
Iout | 3.0 | Maximum Output Current
VinMax | 13.0 | Maximum input voltage
VinMin | 11.0 | Minimum input voltage
Vout | 5.0 | Output Voltage
| base_pn | | TPS563200 | Base Product Number
source | DC | Input Source Type
Ta | 30.0 | Ambient temperature


Copyright © 2020, Texas Instruments Incorporated | 6 | ti.com/webench

## Assembly

## Component Testing

Some published data on components in datasheets such as Capacitor ESR and Inductor DC resistance is based on conservative values that will guarantee that the components always exceed the specification. For design purposes it is usually better to work with typical values. Since this data is not always available it is a good practice to measure the Capacitance and ESR values of Cin and Cout, and the inductance and DC resistance of L1 before assembly of the board. Any large discrepancies in values should be electrically simulated in WEBENCH to check for instabilities and thermally simulated in WebTHERM to make sure critical temperatures are not exceeded.
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

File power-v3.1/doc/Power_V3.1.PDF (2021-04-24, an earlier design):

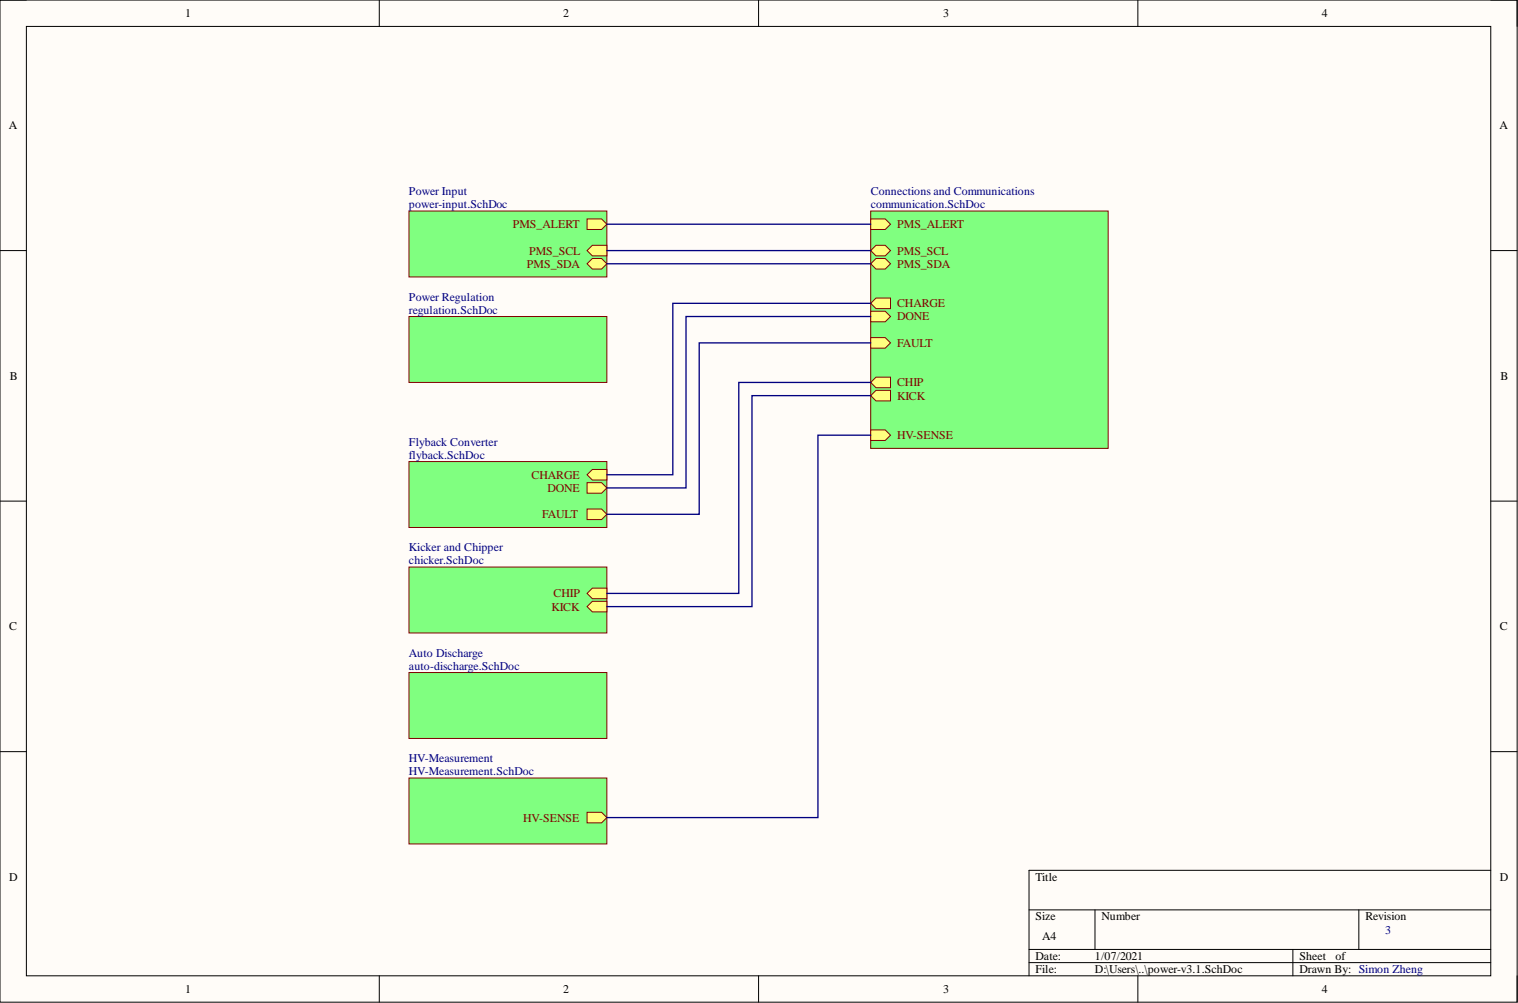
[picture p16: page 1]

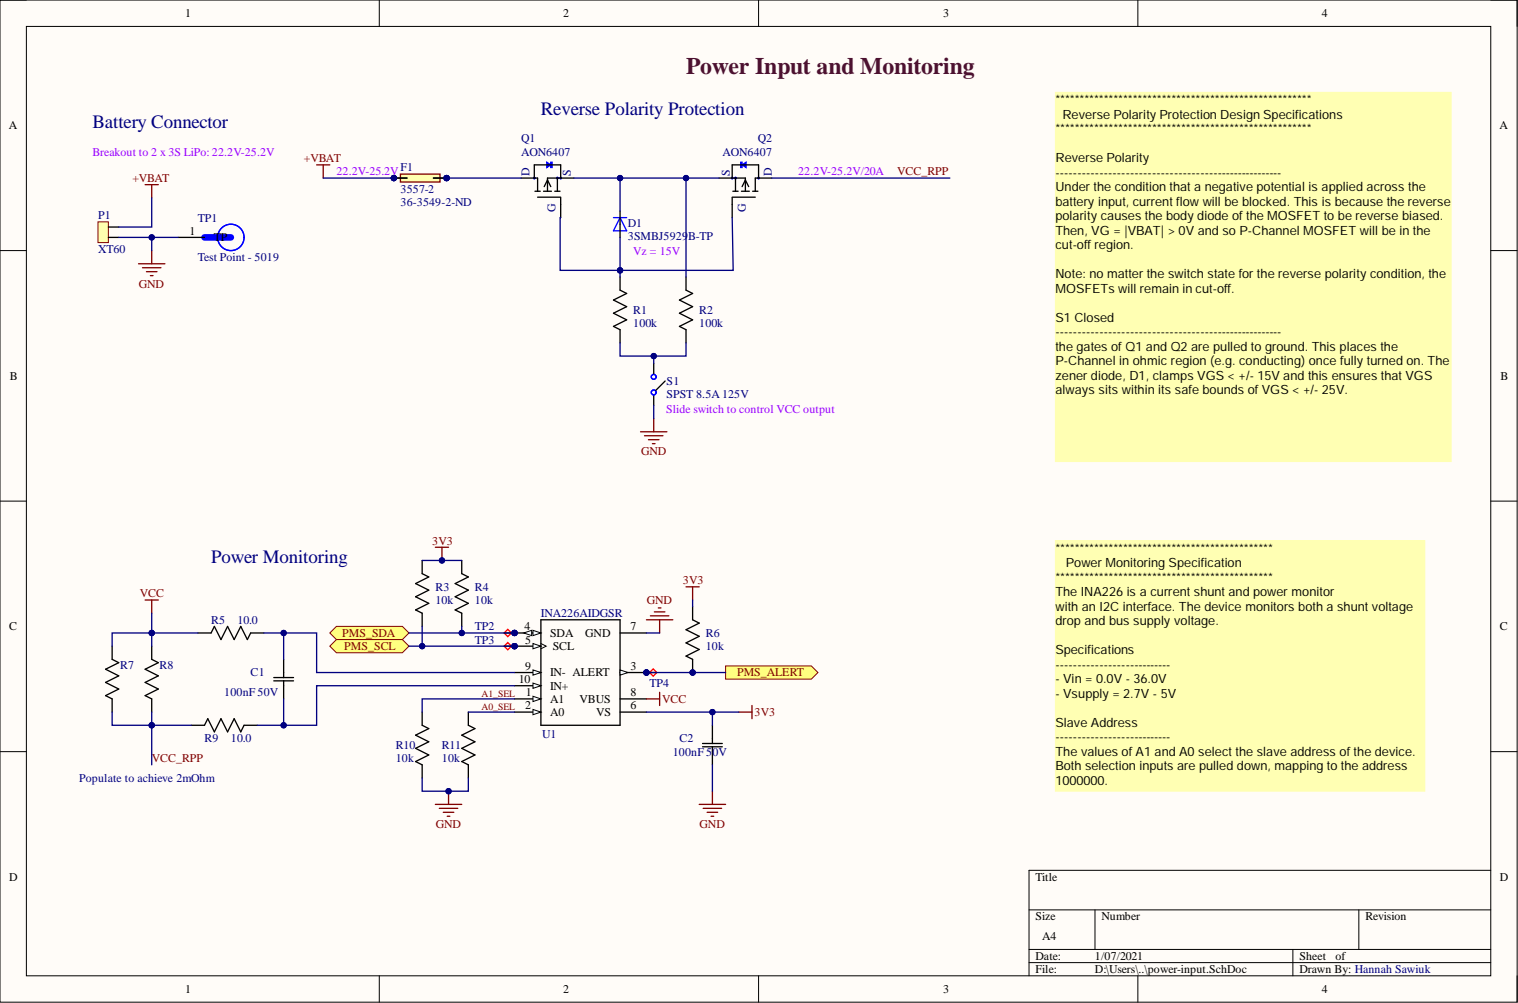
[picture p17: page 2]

Power Input and Monitoring

Reverse Polarity Protection Design Specifications

Reverse Polarity
Under the condition that a negative potential is applied across the
battery input, current flow will be blocked. This is because the reverse
polarity causes the body diode of the MOSFET to be reverse biased.
Then, VG = |VBAT| > 0V and so P-Channel MOSFET will be in the
cut-off region.

Note: no matter the switch state for the reverse polarity condition, the
MOSFETs will remain in cut-off.

S1 Closed
the gates of Q1 and Q2 are pulled to ground. This places the
P-Channel in ohmic region (e.g. conducting) once fully turned on. The
zener diode, D1, clamps VGS < +/- 15V and this ensures that VGS
always sits within its safe bounds of VGS < +/- 25V.

SPST 8.5A 125V
Slide switch to control VCC output

Power Monitoring Specification
The INA226 is a current shunt and power monitor
with an I2C interface. The device monitors both a shunt voltage
drop and bus supply voltage.

IN+ 10
A1 1

A0_SEL | A0 2

Slave Address
The values of A1 and A0 select the slave address of the device.
Both selection inputs are pulled down, mapping to the address


12V DC/DC Converter Spec
Des
des
be found in doc/12V
takes in the batter/suppl

OMs, s
y voltage and steps it down to 12V

mulation exports. and more can
converter

- Vout = 12.0V - Iout = 3.0A - Vripple = 5% - Frequency = 570.0 kHz - Pout = 36.0 W

5V DC/DC Converter Spec
ign report can be found in doc/5V
The converter takes the 12V and steps it down to 5V

ENCH software. The ful

- Vout = 5.0V - Iout = 3.0A - Frequency = 791.515 kHz - Pout = 15.0 W

**************************************** Simple 3.3V fixed LDO for supplying the MCU and various sensors. Specifications --------------------------- - Vin = 1.35V - 18.0V - Vout = 3.3V - Iout = 1.0A - Pout = 3.3W


ides user
kouts for both VCC and VTRANS

s a high input voltage capable fl
y charge a large capac

igned to rapidl
user
ratio and three external res

-adjustable high target voltage set by the transfor

1 6 | RBG R3 5 1.0 5 k


********************************************************************** When VCC drops such that the divided voltage is below BSS127 Vg_th, the STD11 gate is clamped to <15V, draining the +HV rail

See the auto-di
character


No diode in series after the 330k resistors
as the op amp will clamp voltage from
going below 0V.

TVS Diodes are added to protect
against voltage transients from the
inductor switching.


itances, high dV/dt and

-diode reverse recovery can cause unwanted behav
iatel

iate value for the gate res

(1) Rg = R(hi or lo) + Rgate + Rg,i (2) Ls = 1/Ciss(2*pi*f_r)^2 (3) Q = pi*Ls/Rg

Choose qual
(underdamped) See TI's document on "

ign Guide for Gate

BT gates are rated for Vge +/- 20V. To ensure trans

S diodes with a Reverse Wor

ified voltage at whi
cur


1 1
1 3
1 5

Needed for the com
monitor and the MCU gi

muni
ven they are on seperate boards

ines between the power






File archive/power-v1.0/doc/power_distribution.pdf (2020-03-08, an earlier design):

## Battery Connector

## Power Monitoring


Jumpers used to connect 1->2 and 3->4.
Pull-downs to pull to GND if jumpers not
connected.

A1=A0=GND, Slave address is 1000000

Bi-directional EMI Filters

S1 Closed
the gates of Q1 and Q2 are pulled to ground. This places
the P-Channel in ohmic region (e.g. conducting) once
fully turned on. The zener diode, D1, clamps VGS < +/-
15V and this ensures that VGS always sits within its
safe bounds of VGS < +/- 25V.

Reverse Polarity
Under the condition that a negative potential is applied
across the battery input, current flow will be blocked.
This is because the reverse polarity causes the body
diode of the MOSFET to be reverse biased. Then, VG =
VBAT| > 0V and so P-Channel MOSFET will be in the
cut-off region.

Rocker switch to control VCC output

Note: no matter the switch state for the reverse polarity
condition, the MOSFETs will remain in cut-off.

VCC for motor windings, +5V for Hall sensors

Power monitor lines and +3.3V for Nucleo


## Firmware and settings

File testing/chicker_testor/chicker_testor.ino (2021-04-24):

#include "TeensyTimerTool.h"
#include "PulseGen.h"

volatile bool kick_cooldown = true; // flag for kicker grace period, initial TRUE for safety
volatile bool kick = false;

const unsigned TRIG_INDICATOR_PIN = 12;  // pin to indicate when triggering occurs
const unsigned KICKER_PIN = 2;
const unsigned KICK_DELAY = 1'000;        // delay (us)
const unsigned KICK_POWER = 1000;         // pulse width (us)
const unsigned KICK_GRACE_MIN = 100'000;  // minimum time between kicks (us)
const unsigned KICK_INTERRUPT = 30;       // kicker button pin

PulseGen kicker;
IntervalTimer kicker_grace_timer;

void trigger(PulseGen pulse_gen)
{
  digitalWriteFast(TRIG_INDICATOR_PIN, HIGH);

  pulse_gen.trigger();

  digitalWriteFast(TRIG_INDICATOR_PIN, LOW);
}

void kick_ISR()
{
  if(!kick_cooldown){
    kick_cooldown = true;
    kicker.trigger();
    kicker_grace_timer.begin(kick_grace_ISR, KICK_GRACE_MIN);
  }
}

void kick_grace_ISR()
{
  kicker_grace_timer.end();
  kick_cooldown = false;
}

void setup()
{
  pinMode(LED_BUILTIN, OUTPUT);
  pinMode(TRIG_INDICATOR_PIN, OUTPUT);
  pinMode(KICK_INTERRUPT, INPUT_PULLDOWN);
  // TODO: setup serial parsing from PC

  attachInterrupt(digitalPinToInterrupt(KICK_INTERRUPT), kick_ISR, RISING);

  kicker.begin(KICKER_PIN, KICK_DELAY, KICK_POWER);

  kick_cooldown = false;
}

void loop()
{

}

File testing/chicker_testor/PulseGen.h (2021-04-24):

/* Single pulse generator class using the teensy AMR timer tools library

  inputs:
    delayTimer: time between "triggering" and pulse generation
    durationTimer: length of pulse

  Author: Simon Zheng
  */

#include "Arduino.h"
#include "TeensyTimerTool.h"

using namespace TeensyTimerTool;

class PulseGen
{
public:
    PulseGen() : delayTimer(TCK), durationTimer(TCK) // use the tick timers for this task, we have 20 per default, can be increased in config
    {
    }

    void begin(unsigned pin, unsigned delay, unsigned duration)
    {
        this->pin = pin;
        this->delay = delay;
        this->duration = duration;

        pinMode(pin, OUTPUT);
        delayTimer.begin([this] { digitalWriteFast(this->pin,HIGH); this->durationTimer.trigger(this->duration) ; });
        durationTimer.begin([this] { digitalWriteFast(this->pin, LOW); });
    }

    void trigger() { delayTimer.trigger(delay); }

protected:
    unsigned pin, delay, duration;
    OneShotTimer delayTimer, durationTimer;
};

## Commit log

2019-11-14 Moved power pcb project into correct repo
    [PowerBoard.GBL, PowerBoard.GBO, PowerBoard.GBP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]
2019-11-14 Changed many parts to be sourced from Altium Libraries repo
    [PowerBoard_Rev1.SchDoc, power_distrubtion.PrjPCB]
2019-11-14 Updated with Altium Library parts
    [PowerBoard_Rev1.SchDoc]
2019-12-10 LTSpice simulation schematic for RPP
    [PowerBoard_Rev2.SchDoc, power_distrubtion.PrjPCB]
2019-12-24 WIP rev 2, LDO and dc/dc converter todo
    [PowerBoard_Rev1.SchDoc, PowerBoard_Rev2.SchDoc]
2019-12-25 Almost finished rev2 schematic. LDO and COMP inputs to finish
    [PowerBoard_Rev2.SchDoc]
2019-12-26 Updated project name, rev2 final design, pre-review
    [PowerBoard.GBL, PowerBoard.GBO, PowerBoard.GBP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]
2019-12-26 Added Power Board Rev 2 PCB Doc
    [PowerBoard_Rev2.PcbDoc, PowerBoard_Rev2.SchDoc, power_distribution.PrjPCB]
2019-12-26 Updated parts from library
    [PowerBoard_Rev2.SchDoc]
2019-12-26 Fixed some issues
    [PowerBoard_Rev2.PcbDoc, PowerBoard_Rev2.SchDoc]
2019-12-27 Finished Rev2 PCB layout, needs design review
    [PowerBoard_Rev2.PcbDoc, PowerBoard_Rev2.SchDoc]
2019-12-27 Made some small changes
    [PowerBoard_Rev2.PcbDoc]
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2019-12-27 Updated motor power pins and LED resistors
    [PowerBoard_Rev2.SchDoc]
2019-12-28 Widened traces for VCC to allow more current
    [PowerBoard_Rev2.PcbDoc]
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2019-12-30 Updated parts from libraries
    [PowerBoard_Rev2.SchDoc]
2019-12-31 Finished latest pcb layout
    [PowerBoard_Rev2.PcbDoc, PowerBoard_Rev2.SchDoc]
2019-12-31 Fixed top overlay alignment
    [PowerBoard_Rev2.PcbDoc, PowerBoard_Rev2.SchDoc]
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2020-02-29 Added BOM to included
    [power_distribution_rev2_bom.xlsx]
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2020-03-23 Minor updates to simulation. Created Chicker PCB schematic
    [Chicker.PrjPcb, Chicker.SchDoc]
2020-03-24 Rev 1 of Chicker PCB layout
    [Chicker.PcbDoc, Chicker.PrjPcb, Chicker.SchDoc]
2020-03-24 Some things didn't get saved properly in the last commit
    [Chicker.PcbDoc, Chicker.PrjPcb]
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2020-03-25 Small fix to dir structure
    [Chicker.PcbDoc, Chicker.PrjPcb, Chicker.SchDoc]
2020-03-25 Reworked schematic doc structure to reduce merge conflicts
    [Chicker.PcbDoc, Chicker.PrjPcb, Chicker.SchDoc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]
2020-04-20 Added changes discussed in last meeting. Added fuse between VBat and LT3751. Fixed Overvoltage and Undervoltage resistors. Added EMI filters between logic signals and header. Added XT60 header for ba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
    [Flyback.SchDoc]
2020-05-03 reworked structure
    [Flyback.SchDoc, power-io.SchDoc, power-v2.0.PcbDoc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]
2020-05-08 12V dc/dc converter schematic
    [regulation-monitoring.SchDoc]
2020-05-08 Integrated new 12V->5V dc/dc converter
    [power-io.SchDoc, power-v2.1.SchDoc, regulation-monitoring.SchDoc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]
2020-05-08 Saved changes to the project
    [power-v2.1.PrjPCB]
2020-05-09 Finished regulation and input. Output todo
    [power-io.SchDoc, power-v2.1.SchDoc, regulation.SchDoc]
2020-05-09 Moved Flyback to power board schematic
    [flyback.SchDoc, power-io.SchDoc, power-v2.2.PcbDoc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]
2020-05-16 WIP V2 of power
    [chicker.SchDoc, communication.SchDoc, flyback.SchDoc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]
2020-05-16 moved chickerv1.0 and powerv2.1 to archive
    [Chicker.PcbDoc, Chicker.PrjPcb, Flyback.SchDoc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]
2020-05-16 re-added the schematics to the project
    [power-v2.2.SchDoc, regulation.SchDoc]
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2020-06-25 Added IGBT snubber and tvs and connections
    [chicker.SchDoc, communication.SchDoc, flyback.SchDoc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]
2020-11-02 Added HV Measurement Schematic
    [HV-Measurement.SchDoc]
2020-11-21 Updated HV-Measurement Schematic and added Sheet Symbol in power-v2.2 Schematic
    [HV-Measurement.SchDoc, power-v2.2.SchDoc]
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2020-11-24 Operation summary in .sch
    [auto-discharge.SchDoc]
2020-11-27 replaced temp placeholder +HV caps with expected parts
    [flyback.SchDoc]
2020-11-27 Updated new subcircuits (auto-discharge, HV-measure) in top-level schematic, general house-keeping
    [HV-Measurement.SchDoc, auto-discharge.SchDoc, chicker.SchDoc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]
2020-11-27 extended house keeping, correction of some component library references
    [HV-Measurement.SchDoc, auto-discharge.SchDoc, chicker.SchDoc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]
2020-11-27 Refactored working folder and project to power v3.1
    [HV-Measurement.SchDoc, auto-discharge.SchDoc, chicker.SchDoc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]
2020-11-27 added power-v2.2 to archives
    [chicker.SchDoc, communication.SchDoc, flyback.SchDoc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]
2020-11-27 Fixed missing refactor of top_level schematic
    [power-v3.1.SchDoc]
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2020-11-28 Fixed components links for 15V Zener
    [HV-Measurement.SchDoc, auto-discharge.SchDoc, chicker.SchDoc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]
2020-11-28 added dxf and SLDPRT file for power PCB shape
    [Power_pcb.DXF, Power_pcb.SLDPRT]
2020-11-29 Replaced test points
    [HV-Measurement.SchDoc, auto-discharge.SchDoc, chicker.SchDoc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]
2020-11-29 Rough subcircuit block diagram added
    [power-v3.1.PcbDoc, power-v3.1.PrjPCB]
2020-12-06 Added hook style test_points for charge current and flyback primary current and HV
    [flyback.SchDoc]
2020-12-06 modified LT3751 simulation, added larger test points for circuit validation, initial layout
    [HV-Measurement.SchDoc, flyback.SchDoc, power-input.SchDoc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]
2020-12-07 Reverted to DA2034, added more LT3751 decoupling.
    [flyback.SchDoc, power-input.SchDoc, power-v3.1.PcbDoc]
2020-12-07 Initial Power Input and Flyback part positioning, expanded rooms for part staging
    [HV-Measurement.SchDoc, auto-discharge.SchDoc, chicker.SchDoc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]
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2020-12-10 IGBT stage layout ideas
    [chicker.SchDoc, flyback.SchDoc, power-v3.1.PcbDoc]
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2020-12-13 Moved to single XT60 connector, experimental power input layout changes
    [auto-discharge.SchDoc, communication.SchDoc, flyback.SchDoc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]
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2020-12-25 Reworked location of HV components and DC regulators
    [flyback.SchDoc, power-input.SchDoc, regulation.SchDoc]
2020-12-25 Minor polygon additions, GND on regulation LED indicators
    [regulation.SchDoc]
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2020-12-27 removed some test-points due to space constraints; via stiching added to GND, test HV guard trace
    [chicker.SchDoc, power-v3.1.PrjPCB, regulation.SchDoc]
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2020-12-28 Fixed PMIC VBUS circuit error; moved IGBT block; GND GND GND GND
    [communication.SchDoc, power-input.SchDoc]
2020-12-28 Added HV-meas layout, fixed HV-Sense naming scheme, fixed small connectivity issues in HV-meas schematic
    [HV-Measurement.SchDoc, communication.SchDoc]
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2021-01-04 Minor silkscreen correction, cap position relocated for shell standoff, lower mounting hole location changes.
    [auto-discharge.SchDoc, flyback.SchDoc]
2021-01-04 Shell standoff cut-out polygon clearance centering
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2021-01-06 Converted mounting vias to circular pth pads for correct CAD generation
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2021-01-06 Typo correction
    [HV-Measurement.SchDoc, auto-discharge.SchDoc, flyback.SchDoc]
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2021-01-06 Fixed flyback done, fault signals to 3V3 pullup
    [flyback.SchDoc]
2021-01-08 Doubled up input sense resistance footprint for versatility
    [HV-Measurement.SchDoc, auto-discharge.SchDoc, chicker.SchDoc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]
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2021-01-11 Tapered front edge in-board, added active BOM to track substitutes
    [power-v3.1.PrjPCB]
2021-01-12 Changed T1 decoupling caps to 1210 for cost and sourcing
    [flyback.SchDoc]
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2021-01-19 fixed fault - done order
    [communication.SchDoc, flyback.SchDoc, power-v3.1.PrjPCB]
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2021-05-04 Changed interboard signal connector, changed component sizing of regulation state, added pot to LT4751 RBG
    [HV-Measurement.SchDoc, auto-discharge.SchDoc, chicker.SchDoc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]
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2021-05-14 modified power connector pin out for simplified routing
    [communication.SchDoc, power-v3.2.PrjPCB]
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2021-05-15 Flipped external capacitor connectors onto top-side to clear chipper mounting holes
2021-06-08 added isolator side pull downs on Charge, Kick, Chip. Reverted RBG to 1.05k
    [communication.SchDoc, flyback.SchDoc, power-v3.2.PrjPCB]
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2021-09-03 replaced 5V regulator inductor with fully shielded inductor
    [regulation.SchDoc]
2021-09-13 replaced gate driver IC and reviewed chicker schematic
    [chicker.SchDoc]
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2021-09-23 Replaced Power Monitor and Updated Schematic
    [power-input.SchDoc]

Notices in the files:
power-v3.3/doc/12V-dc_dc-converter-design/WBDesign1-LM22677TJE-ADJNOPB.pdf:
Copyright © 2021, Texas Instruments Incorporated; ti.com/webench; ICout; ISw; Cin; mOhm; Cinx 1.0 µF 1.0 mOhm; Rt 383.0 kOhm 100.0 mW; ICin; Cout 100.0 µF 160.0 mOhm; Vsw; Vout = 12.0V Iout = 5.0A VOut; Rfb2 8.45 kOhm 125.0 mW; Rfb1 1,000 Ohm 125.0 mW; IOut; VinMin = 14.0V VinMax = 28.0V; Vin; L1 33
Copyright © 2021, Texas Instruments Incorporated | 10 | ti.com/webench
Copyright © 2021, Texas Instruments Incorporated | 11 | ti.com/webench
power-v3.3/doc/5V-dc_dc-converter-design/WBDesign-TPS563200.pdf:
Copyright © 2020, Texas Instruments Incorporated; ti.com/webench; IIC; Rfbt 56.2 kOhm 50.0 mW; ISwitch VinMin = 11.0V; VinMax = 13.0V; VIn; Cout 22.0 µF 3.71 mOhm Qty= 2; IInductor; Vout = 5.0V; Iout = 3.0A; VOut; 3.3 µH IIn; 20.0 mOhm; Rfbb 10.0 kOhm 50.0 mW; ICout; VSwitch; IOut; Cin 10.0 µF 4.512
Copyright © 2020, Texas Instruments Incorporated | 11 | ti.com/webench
